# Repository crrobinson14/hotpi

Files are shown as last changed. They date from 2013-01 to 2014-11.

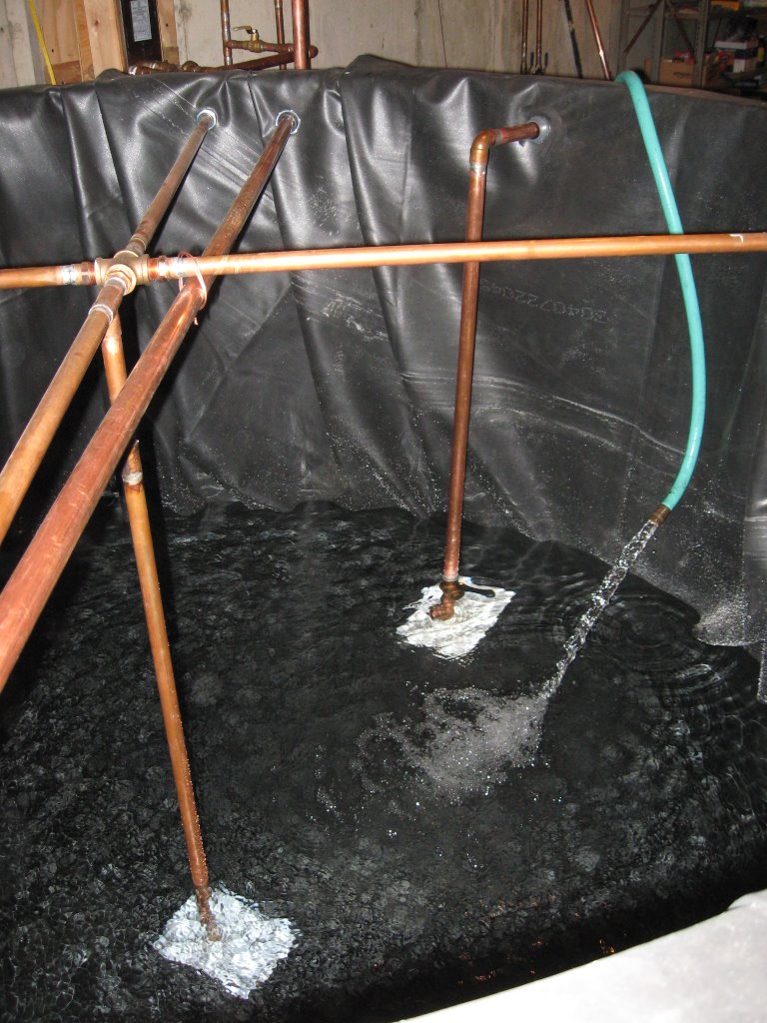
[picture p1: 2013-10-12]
photos/05 Lid Support.JPG

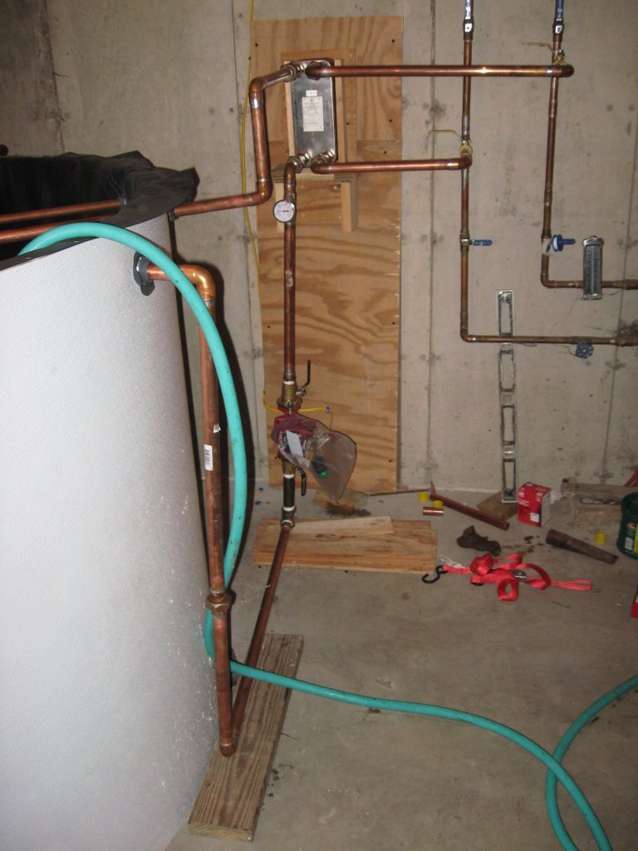
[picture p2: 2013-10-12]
photos/06 FlatPlate Plumbing.JPG

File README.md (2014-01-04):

hotpi
=====

HotPi is a Raspberry-Pi based heating control system. It is
designed to manage wood boilers, solar arrays, and other
alternative energy sources, although it is generic enough
that it could be programmed to control near any heating
and/or cooling system.

HotPi is Open Source Hardware (OSHW). That means it is not
a product - you must build it yourself, and you are solely
liable for its installation and programming. Included in
this project are circuit schematics, PCB layouts (with
Gerber files) for producing the boards, components lists,
documentation, and sample software.

For more information please see the project wiki:
https://github.com/crrobinson14/hotpi/wiki

LEGAL NOTICE: No warranties are made, expressed or implied,
as to the usability, merchantability, or performance of the
hardware or software provided in this project. All use is at
your own risk.

Analytics (https://github.com/igrigorik/ga-beacon)

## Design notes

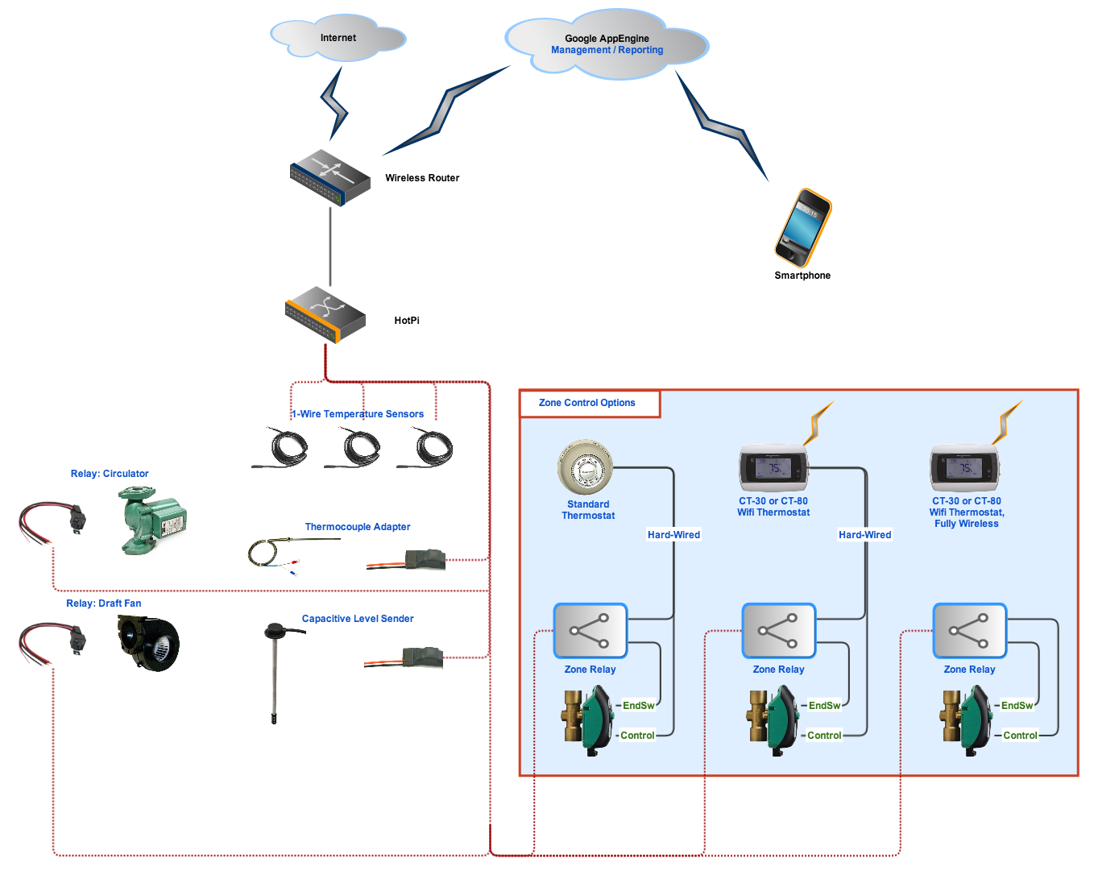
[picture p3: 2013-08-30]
docs/images/Overview.png

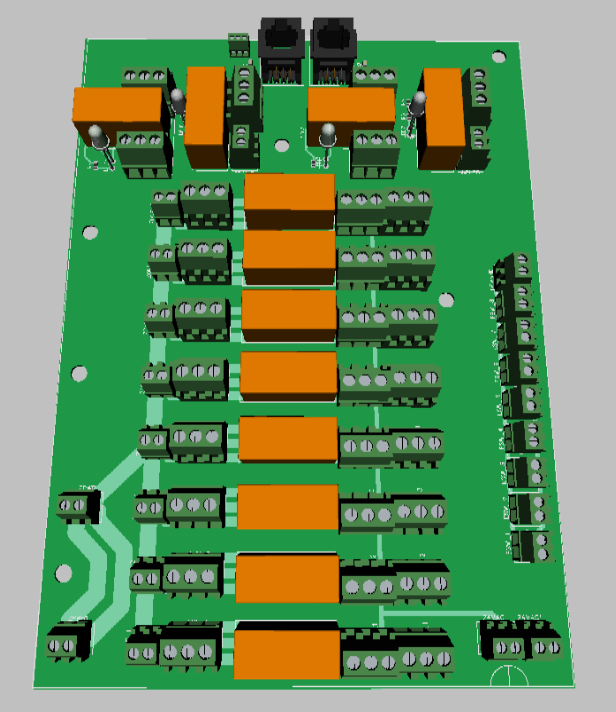
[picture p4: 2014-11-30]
pcb/zone/zone.png

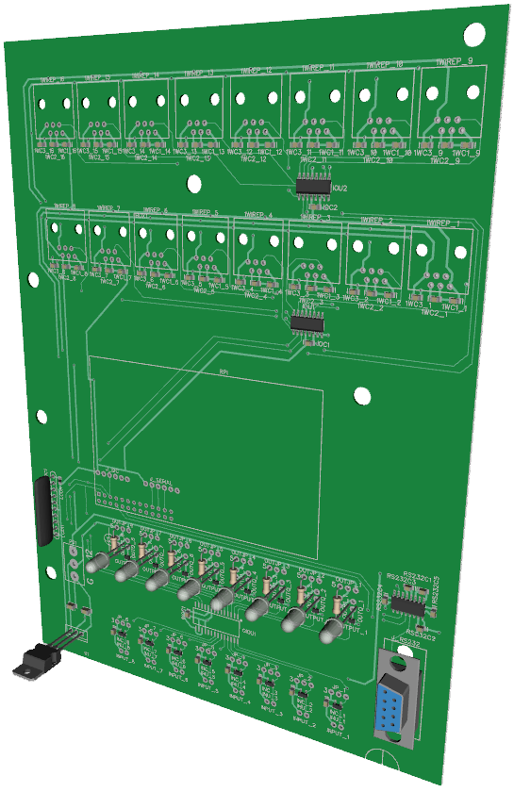
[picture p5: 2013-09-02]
pcb/hotpi/hotpi-3d.png

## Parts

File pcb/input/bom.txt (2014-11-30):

"RefDes","Value","Quantity","PartNumber"
"1WIRE2","","1","A-2014-1-4-R"
"C1","1u","1","C2012X7S2A105K"
"C2","0.1u","1","C0805C104K3RACTU"
"INPUT","","1",""
"LED1","GRN 2.2V 10mA","1","WP7113GD"
"R1","200","1","RMCF0805FT200R"
"R2","120","1","ERJ-6ENF1200V"
"RLY1","","1","RT424524"
"U2","","1","DS2413P+"

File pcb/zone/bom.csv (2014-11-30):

RefDes | Value | Quantity | PartNumber
1WACC |  | 1
1WIRE1 |  | 1 | A-2014-1-4-R
1WIRE2 |  | 1 | A-2014-1-4-R
24VAC |  | 1 | 282841-2
24VAC1 |  | 1 | 282841-2
AUX |  | 8 | 282841-3
BOX1 |  | 1 | TL412CP
C1 | 1u | 1 | C2012X7S2A105K
C2 | 0.1u | 1 | C0805C104K3RACTU
D3 |  | 1 | S1M-FDICT
D4 |  | 1 | S1M-FDICT
DEMAND |  | 1 | 282841-2
ESW |  | 8 | 282841-2
INPUTA |  | 1
INPUTB |  | 1
LED1 | GRN 2.2V 10mA | 1 | WP7113GD
LED2 | GRN 2.2V 10mA | 1 | WP7113GD
LED3 | ORG 2V 10mA | 1 | SLR-56DC3F
LED4 | ORG 2V 10mA | 1 | SLR-56DC3F
OUT1A |  | 1
OUT1B |  | 1
OUT2A |  | 1
OUT2B |  | 1
P1 |  | 1
P2 |  | 1
Q2 |  | 1 | DDTA113ZCA-7-F
Q3 |  | 1 | DDTA113ZCA-7-F
R1 | 1k 1/4W | 1 | RNCP0805FTD1K00
R2 | 120 | 1 | ERJ-6ENF1200V
R3 | 120 | 1 | ERJ-6ENF1200V
R4 | 1k 1/4W | 1 | RNCP0805FTD1K00
R5 | 200 | 1 | RMCF0805FT200R
R6 | 200 | 1 | RMCF0805FT200R
RLY1 |  | 1
RLY2 |  | 1 | RT424012
RLY3 |  | 1 | RT424524
RLY4 |  | 1 | RT424524
RLY6 |  | 8
TB |  | 8 | 282841-3
TT |  | 8 | 282841-3
U1 |  | 1 | DS2413P+
U2 |  | 1 | DS2413P+
ZONE |  | 8 | 282841-2
ZPWR |  | 1 | 282841-2
ZPWR1 |  | 1 | 282841-2

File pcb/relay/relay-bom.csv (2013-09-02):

# | Quantity | Type | Value | PartNumber | RefDes
1 | 1 | JP3 |  |  | 1WACC
2 | 2 | RJ12 |  | A-2014-1-4-R | 1WIRE1, 1WIRE2
3 | 1 | CAP_0805 | 1u | C2012X7S2A105K | C1
4 | 1 | CAP_0805 | 0.1u | C0805C104K3RACTU | C2
5 | 1 | 1N4007 |  | S1M-FDICT | D1
6 | 1 | TERM2 |  |  | INPUT
7 | 1 | JP6 |  |  | JP1
8 | 1 | LED | GRN 2.2V 10mA | WP7113GD | LED1
9 | 1 | LED | ORG 2V 10mA | SLR-56DC3F | LED2
10 | 3 | TERM3 |  |  | OUTPUT1, OUTPUT2, P1
11 | 1 | DDTA113 |  | DDTA113ZCA-7-F | Q4
12 | 1 | RES_0805 | 200 | RMCF0805FT200R | R1
13 | 1 | RES_0805 | 120 | ERJ-6ENF1200V | R2
14 | 1 | RES_0805 | 1k 1/4W | RNCP0805FTD1K00 | R3
15 | 1 | RT2 |  | RT424524 | RLY1
16 | 1 | RT1 |  | RT424012 | RLY2
17 | 1 | DS2413 |  | DS2413P+ | U2
 | 20

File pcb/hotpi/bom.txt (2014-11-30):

"RefDes","Value","Quantity","PartNumber"
"1WC1","0.1u","16","C0805C104K3RACTU"
"1WC2","0.1u","16","C0805C104K3RACTU"
"1WC3","0.1u","16","C0805C104K3RACTU"
"1WIREP","","16","A-2014-1-4-R"
"BOX1","","1","TL412CP"
"C1","10u TANT","1","399-3684-1"
"C2","10u TANT","1","399-3684-1"
"IOC1","0.1u","1","C0805C104K3RACTU"
"IOC2","0.1u","1","C0805C104K3RACTU"
"IOU1","","1","DS2482S-800"
"IOU2","","1","DS2482S-800"
"PS1","","1","282841-3"
"U1","3.3V","1","LM1117T-3.3/NOPB"
"U2","","1",""
"U3","","1",""

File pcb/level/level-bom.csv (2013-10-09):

# | Quantity | Type | Value | PartNumber | RefDes
1 | 2 | JP3 |  |  | JP1, JP2
2 | 12 | RES_0805 | 470 | RMCF0805FT470R | R1, R2, R3, R4, R5, R6, R7, R8, R9, R10, R11, R12
3 | 12 | REED |  | ORD324-1015 | SW1, SW2, SW3, SW4, SW5, SW6, SW7, SW8, SW9, SW10, SW11, SW12
 | 26

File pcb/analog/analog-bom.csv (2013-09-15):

# | Quantity | Type | Value | PartNumber | RefDes
1 | 3 | JP3 |  |  | 1WACC, JP2, JP3
2 | 2 | RJ12 |  | A-2014-1-4-R | 1WIRE1, 1WIRE2
3 | 1 | CAP_0805 | 1u | C2012X7S2A105K | C1
4 | 6 | CAP_0805 | 0.1u | C0805C104K3RACTU | C2, C3, C9, C10, C12, C13
5 | 1 | CAP_0805 | 10u TANT | 399-3684-1 | C11
6 | 1 | JP6 |  |  | JP1
7 | 2 | TERM2 |  | 282841-2 | P1, P2
8 | 1 | RES_1206 | .02 | LVK24R020DER | R1
9 | 2 | RES_0805 | 0.30 | 311-.30SCT | R2, R5
10 | 1 | RES_0805 | 1M | RMCF0805FT1M00CT | R7
11 | 1 | DS2756E+ |  | DS2756E+ | U1
12 | 1 | AD849x |  | AD8495ARMZ | U2
 | 22

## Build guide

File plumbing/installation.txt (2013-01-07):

Oil Boiler
----------
1. Install a pair of 1" Tees (A) on the inlet/outlet of the oil boiler. On the
outlet side, this may also require a new 1" MIP to sweat (B).

2. Plumb both Tees with 1" copper pipe (C) to a pair of 1" sweat-to-PEX adapters
(D), then with 1" PEX (E) to a pair of ball valves (F).

3. Cut the 1/2" cold water supply line to the furnace at a convenient spot along
its horizontal run. Cut the pipe again in the vertical section to remove the
double-elbow transition from horizontal to vertical.

4. Assemble a short "H" bypass with a ball valve (F) and two Tees (Q). Add a
pair of ball valves (F) on the top of each leg.

5. Solder a Tee (I) onto the horizontal run, then run a vertical pipe (J) to a
1/2"-1" reducer (K) and fitting (D) into one leg of the bypass. Plumb the
vertical inlet line to the other bypass leg using a reducer (K) and fitting (D).

5. Cut the cold water inlet to the mixing valve just past the elbow below the
valve. Cap (L) the remaining section past the low-water drain valve.

6. De-solder the elbow from the cold water inlet to retain as much stub as
possible, and clean up the end (discard the elbow). Rotate the stub to a
45-degree angle and use a coupling (M) and elbow (N) to plumb this to the cold
water supply Tee.

7. Plumb PEX lines from all four ball valves over to the hot water storage tank
using tube supports (O) and bend supports (P). On the boiler lines, install a
pair of check valves (G) with fittings (H) such that the flow arrow points
TOWARD the boiler on the HOT line, and the flow arrow points AWAY from the
boiler on the COLD line.

8. For now, close all four ball valves leading to the hot water storage tank,
then open the ball valve between the Tees on the DHW coil inlet. Re-charge the
system and verify that the oil boiler correctly heats the house and hot water.

A - 2 - 1" Copper Tee - http://www.pexsupply.com/Cello-WPT-16-1-CxCxC-Tee-1056000-p
B - 1 - 1" MIP to sweat - http://www.pexsupply.com/Cello-WP4-16-1-Copper-X-Male-Adapter-1024000-p
C - 1 - 1" x 2' Copper Pipe - http://www.pexsupply.com/Kobe-Wieland-100-20-MCP-1-x-2-Type-M-Straight-Copper-Pipe
D - 4 - 1" Sweat to PEX - http://www.pexsupply.com/HydroPEX-H021000-1-PEX-x-1-Copper-Pipe-Brass-Adapter-3755000-p
E - 1 - 1" Barrier PEX - http://www.pexsupply.com/Rifeng-100-300-OXY-1-Oxygen-Barrier-PEX-Tubing-300-ft-Coil
F - 5 - 1" Ball Valve - http://www.pexsupply.com/HydroPEX-H081000-1-PEX-x-1-PEX-Ball-Valve-5882000-p
G - 2 - Check Valve - http://www.pexsupply.com/Hydrovalve-SC100T-1-Threaded-Swing-Check-Valve
H - 4 - 1" MIP to PEX - http://www.pexsupply.com/HydroPEX-H031000-1-PEX-x-1-NPT-Brass-Male-Adapter-3747000-p
I - 1 - 1/2" Copper Tee - http://www.pexsupply.com/Cello-WPT-08-1-2-CxCxC-Tee-1054000-p
J - 1 - 5' 1/2" Copper Pipe - http://www.homedepot.com/h_d1/N-5yc1v/R-100558487/h_d2/ProductDisplay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
K - 2 - 1/2" to 1" Sweat - http://www.pexsupply.com/Cello-WP0-16-08-1-x-1-2-CxC-Coupling-3588000-p
L - 1 - 1/2" Cap - http://www.pexsupply.com/Cello-WP17-08-1-2-Copper-Cap-951000-p
M - 1 - 1/2" Copper Coupling - http://www.pexsupply.com/Cello-WP0-08-1-2-CxC-Coupling-1188000-p
N - 1 - 1/2" Elbow - http://www.pexsupply.com/Cello-WP7-08-1-2-CxC-90-Elbow-896000-p
O - 1 - 1" Tube Support, Box - http://www.pexsupply.com/Sioux-Chief-555-4-Tube-Talon-for-1-PEX-Tubing-Bag-of-50-2207000-p
P - 8 - 1" Bend Support - http://www.pexsupply.com/Viega-51060-1-PEX-Plastic-Bend-Support-12534000-p
Q - 2 - 1" PEX Tee - http://www.pexsupply.com/HydroPEX-H051000-1-PEX-x-1-PEX-x-1-PEX-Brass-Tee-3728000-p

Storage Tank
------------
1. Plumb the boiler "hot" line into the outlet side of an air scoop (A) using a
pair of 1" fittings (B). Install a vent (C) and expansion tank (D) on the air
scoop.

2. On both hot and cold above the tank, add a pair of Tees (E) horizontally,
with the stubs pointing down at a convenient point to run down to the tank. Put
a ball valve (F) on the other side of each Tee. Do the same for the domestic hot
water, but use elbows instead (G).

3. Fabricate a DHW heat exchanger by cutting a 6-port manifold (H) in half and
capping (I) one cut end, then installing a pair of sweat fittings (J). Cut one
7' and two 8.5' lengths from a coil of 1/2" tubing (K) and solder these
between the two manifolds, bending the two longer lengths outward as necessary.
Suspend this coil in the tank approx. 6" below the top lip.

4. Plumb this heat exchanger through two bends and a pair of elbows (G) out
through holes in the top lip of the tank and then up to the DHW hot/cold lines.

5. Fabricate the boiler heat exchanger coils by cutting the remaining tubing
into two 18' lengths, and then the next coil into two 24' lengths and two 6'
lengths. Coil these tubes as necessary to service the four corners and two long
sides of the tank. Solder these to two more manifolds (H).

6. Plumb both manifolds similarly to the DHW setup, using sweat fittings (J) to
run the lines out to a pair of elbows (G), but add an additional elbow on the
bottom (cold) line to make the direction change. Also, insulate (L) the cold
line as much as possible. Run the "hot" line directly up to the appropriate Tee.

7. On the cold side, run the line back down again outside the tank to a Tee (E)
and then to a pair of elbows (G) to create two branches. Connect one leg to a
zone valve (M) using a pair of fittings (B), with the flow direction pointing
DOWN. Connect the other leg to a circulator (N) using a pair of flanges (O)
and fittings (B).

8. Connect both branches down to the stubs of a pair of Tees (E). Connect these
Tees together, then run one line to a ball valve (F) low point drain, and the
other through an elbow (G) and up to the hot-line Tee.

9. Use 1/2" CPVC tubing plus Tee and Elbow fittings to build a support framework
for the heat exchangers. Then build two 1" CPVC stubs with elbows through the
top lip of the tank. One stub should go nearly to the bottom of the tank
(intake) while the other should end as close to the top of the tank as possible.

10. Build a thermostat dip tube from 1/2" CPVC by capping one end and using an
elbow on the other. Install two temperature sensors in the tube, one near the
top and the other near the bottom, with heat-shrink on the connections to
prevent them from shorting one another out. Fill the tube with mineral oil.

11. Seal all tank holes with silicone. Slowly charge each heat exchanger and
check carefully for leaks. Fix any leaks, using compressed air to blow out the
lines if necessary. Then fill the tank and check the tank itself for leaks. Once
everything is ready to go, close back off the oil burner heat lines but leave
the DHW lines open.

A - 1 - Air Scoop - http://www.pexsupply.com/Taco-431-6-1-Air-Scoop-3512000-p
B - 6 - 1" MIP to PEX - http://www.pexsupply.com/HydroPEX-H031000-1-PEX-x-1-NPT-Brass-Male-Adapter-3747000-p
C - 1 - Air Vent - http://www.pexsupply.com/Taco-400-4-1-8-Hy-Vent
D - 1 - Exp. Tank - http://www.ebay.com/itm/Flexcon-HTX-30-4-1-2-gal-Hydronic-Expansion-Tank-/130746785428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
E - 5 - 1" PEX Tee - http://www.pexsupply.com/HydroPEX-H051000-1-PEX-x-1-PEX-x-1-PEX-Brass-Tee-3728000-p
F - 3 - 1" Ball Valve - http://www.pexsupply.com/HydroPEX-H081000-1-PEX-x-1-PEX-Ball-Valve-5882000-p
G - 10 - 1" PEX Elbow - http://www.pexsupply.com/HydroPEX-H001000-1-PEX-x-1-PEX-Brass-Elbow-3701000-p
H - 3 - 6-port Manifold - http://www.ebay.com/itm/6-Outlet-Copper-Manifold-by-Alberta-Custom-Tee-1-x-6-1-2-Ports-/190663487818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
I - 1 - 1" Cap - http://www.pexsupply.com/Cello-WP17-16-1-Copper-Cap-953000-p
J - 4 - 1" Sweat to PEX - http://www.pexsupply.com/HydroPEX-H021000-1-PEX-x-1-Copper-Pipe-Brass-Adapter-3755000-p
K - 2 - 1/2" 60' Tubing - http://www.homedepot.com/Plumbing-Pipes-Fittings-Valves-Copper-Pipe-Fittings-Pipe/h_d1/N-25ecodZ5yc1vZ25ecodZ25ecodZ25ecodZbuyt/R-202504352/h_d2/ProductDisplay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
L - ? - Insulation - http://www.lowes.com/pd_24434-1410-P12XB/6_0__?productId=3133247
M - 1 - Zone Valve - http://www.pexsupply.com/Taco-Z100T2-1-1-Zone-Sentry-Valve-Threaded
N - 1 - Taco 007 - http://www.pexsupply.com/Taco-007-F5-007-Cast-Iron-Circulator-1-25-HP-1983000-p
O - 1 - Taco Flange - http://www.pexsupply.com/Taco-110-252F-1-Taco-Iron-Freedom-Flange-Pair-1974000-p

Wood Boiler
-----------
1. Plumb the hot-side line above the wood boiler and into a Tee (A) with the
stub pointing to the right. Connect the bottom of the Tee into the boiler via
a threaded fitting (B). Stub the Tee over to the right side of the boiler,
through an elbow, and down to a zone valve (D) via a pair of fittings (B).
The flow direction on the zone valve should point down.

2. Plumb the cold-side line across to the right side of the wood boiler and
down nearly (6") to the floor, into the stub of a Tee (A). Connect the right
side of the Tee to a ball valve (E) low point drain. Connect the left side to
the right side of another Tee (A). The stub of this Tee should connect to the
zone valve from Step 1 above.

3. Connect the next leg of the tees into an elbow and up into a circulator (F)
via a flange (G) and a pair of fittings (B). Support the circulator with a block
of wood.

4. Connect the top of the circulator through a pair of elbows (C) around the
back of the wood boiler and into a Tee (A) and a final elbow (C) and into the
inlets of the boiler via a pair of fittings (B).

5. Install a relief valve on a short iron pipe stub in the pressure-relief hole
on top of the boiler.

6. Connect the boiler's flue as required.

7. Fill the boiler with water and check for leaks in the entire system. Then
test fire the boiler with a SMALL load of wood with a thermometer in the
temperature well in the top of the water jacket. If the temperature reaches an
unacceptable level, force the circulator to turn on and dump heat into the water
tank.

A - 4 - 1" PEX Tee - http://www.pexsupply.com/HydroPEX-H051000-1-PEX-x-1-PEX-x-1-PEX-Brass-Tee-3728000-p
B - 7 - 1" MIP to PEX - http://www.pexsupply.com/HydroPEX-H031000-1-PEX-x-1-NPT-Brass-Male-Adapter-3747000-p
C - 4 - 1" PEX Elbow - http://www.pexsupply.com/HydroPEX-H001000-1-PEX-x-1-PEX-Brass-Elbow-3701000-p
D - 1 - Zone Valve - http://www.pexsupply.com/Taco-Z100T2-1-1-Zone-Sentry-Valve-Threaded
E - 3 - 1" Ball Valve - http://www.pexsupply.com/HydroPEX-H081000-1-PEX-x-1-PEX-Ball-Valve-5882000-p
F - 1 - Taco 007 - http://www.pexsupply.com/Taco-007-F5-007-Cast-Iron-Circulator-1-25-HP-1983000-p
G - 1 - Taco Flange - http://www.pexsupply.com/Taco-110-252F-1-Taco-Iron-Freedom-Flange-Pair-1974000-p
H - 1 - Relief Valve - Home Depot
Z - 1 - 3/4" Iron Pipe - Home Depot

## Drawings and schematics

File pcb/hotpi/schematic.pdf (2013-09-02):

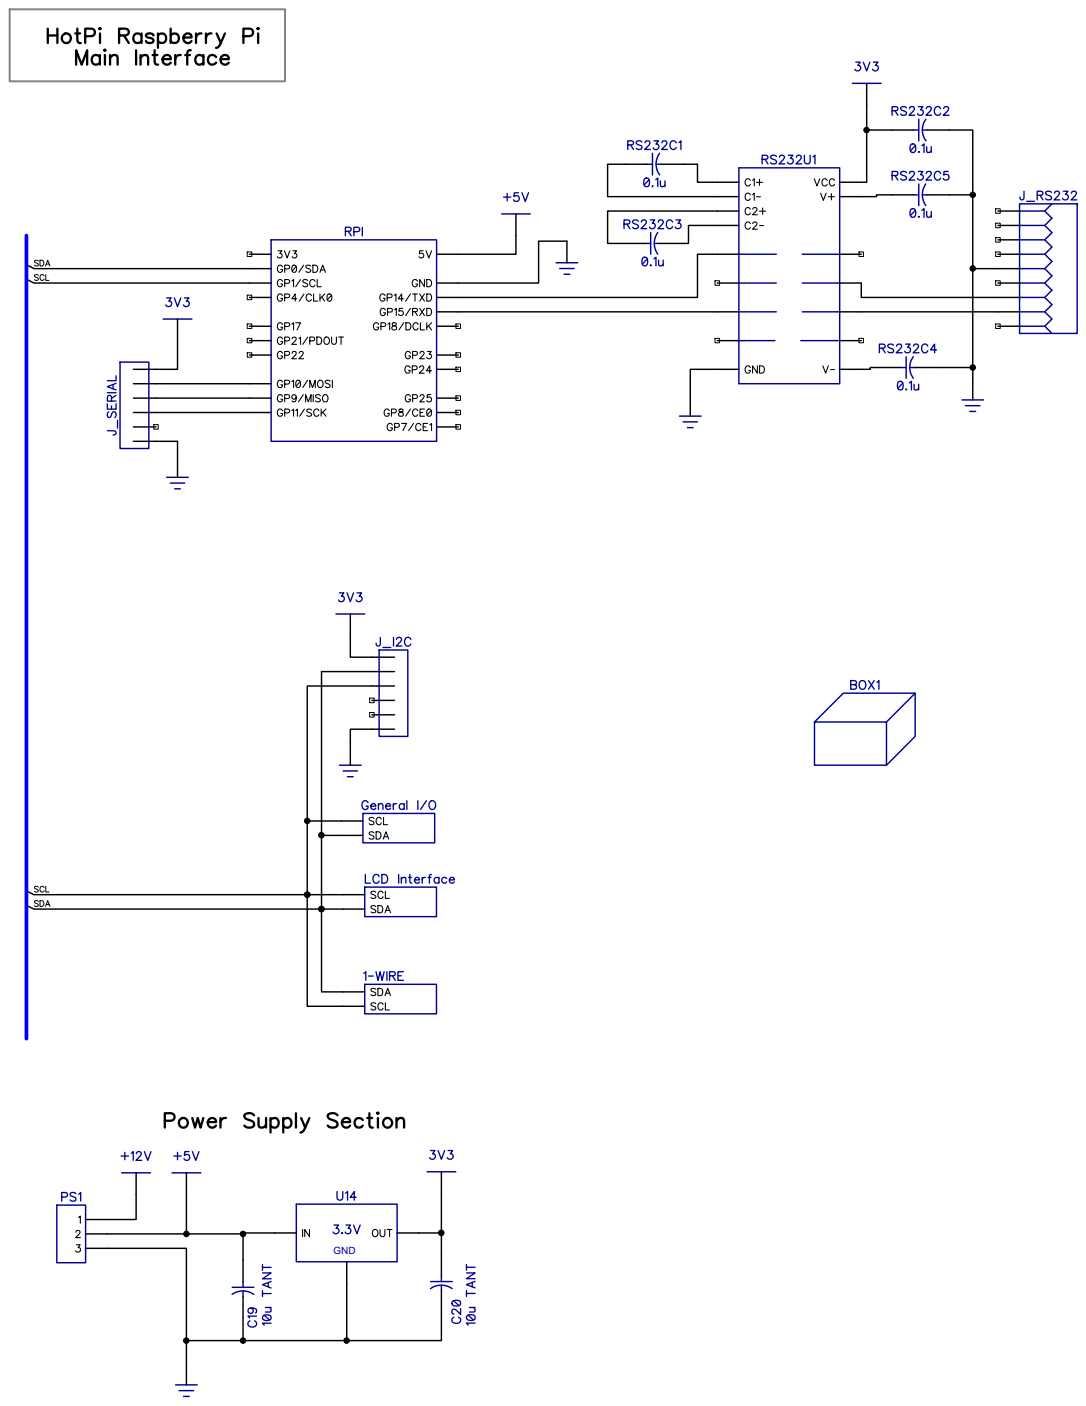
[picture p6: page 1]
GND

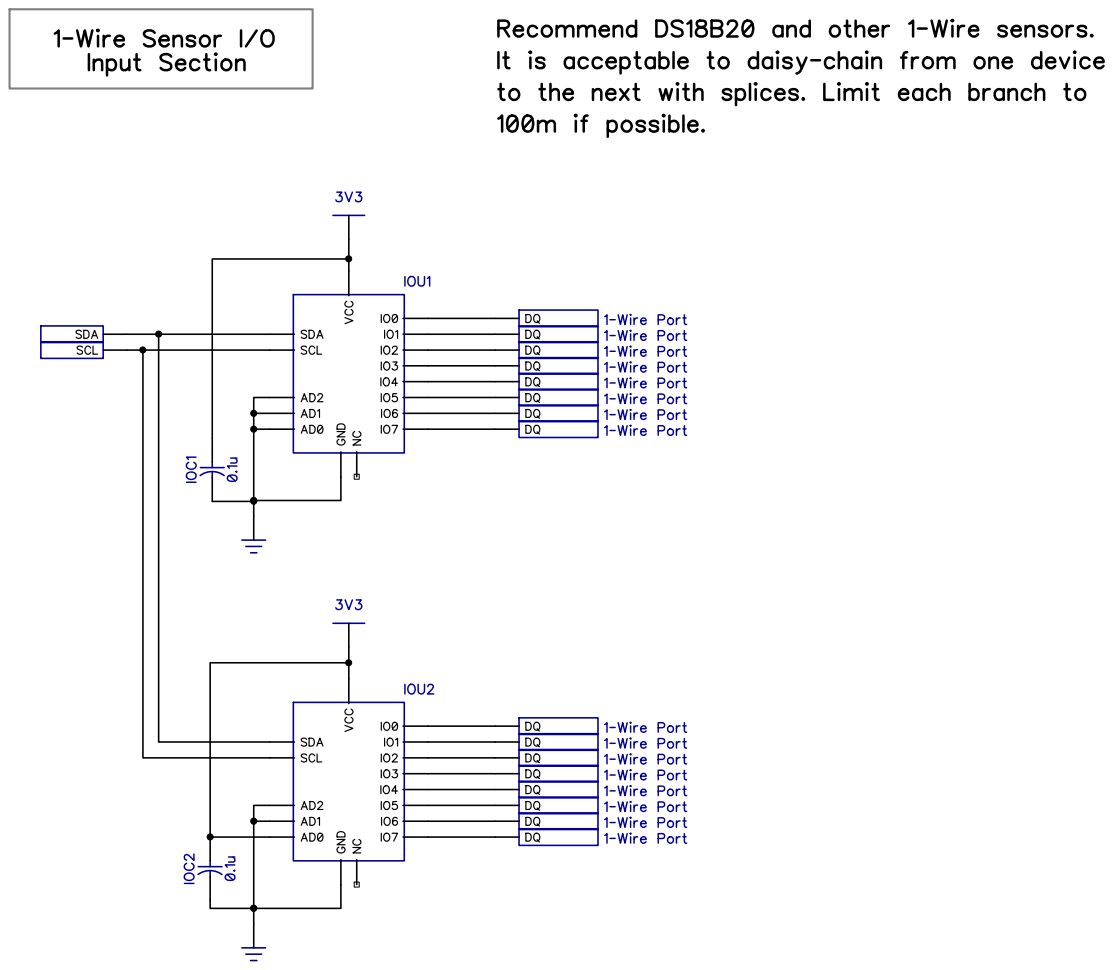
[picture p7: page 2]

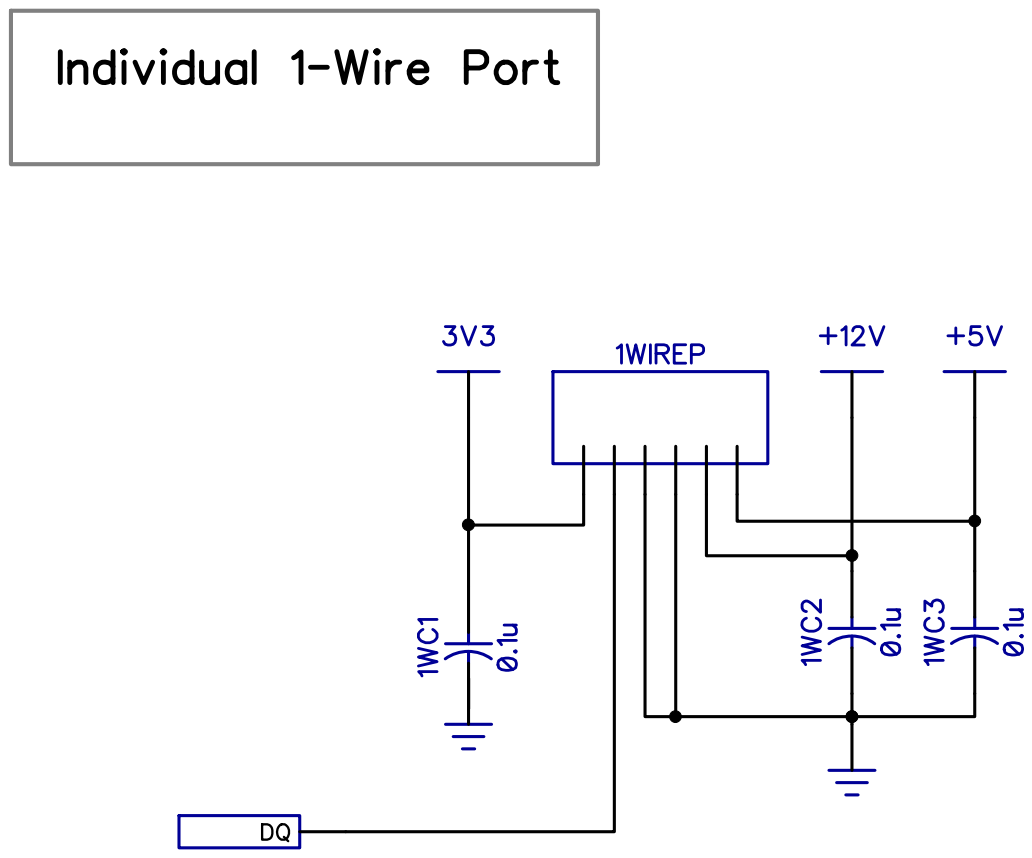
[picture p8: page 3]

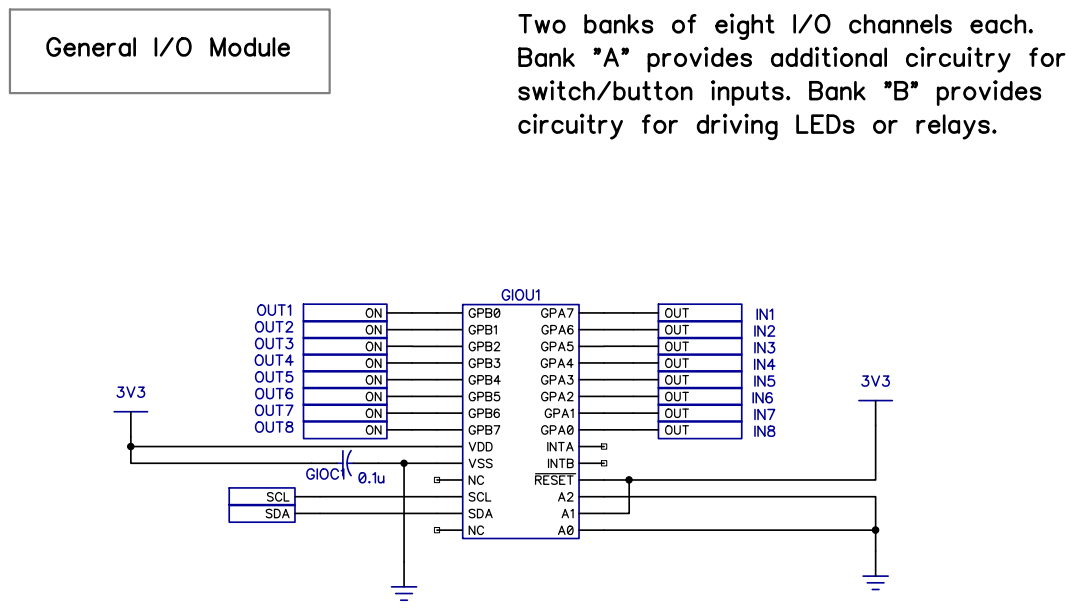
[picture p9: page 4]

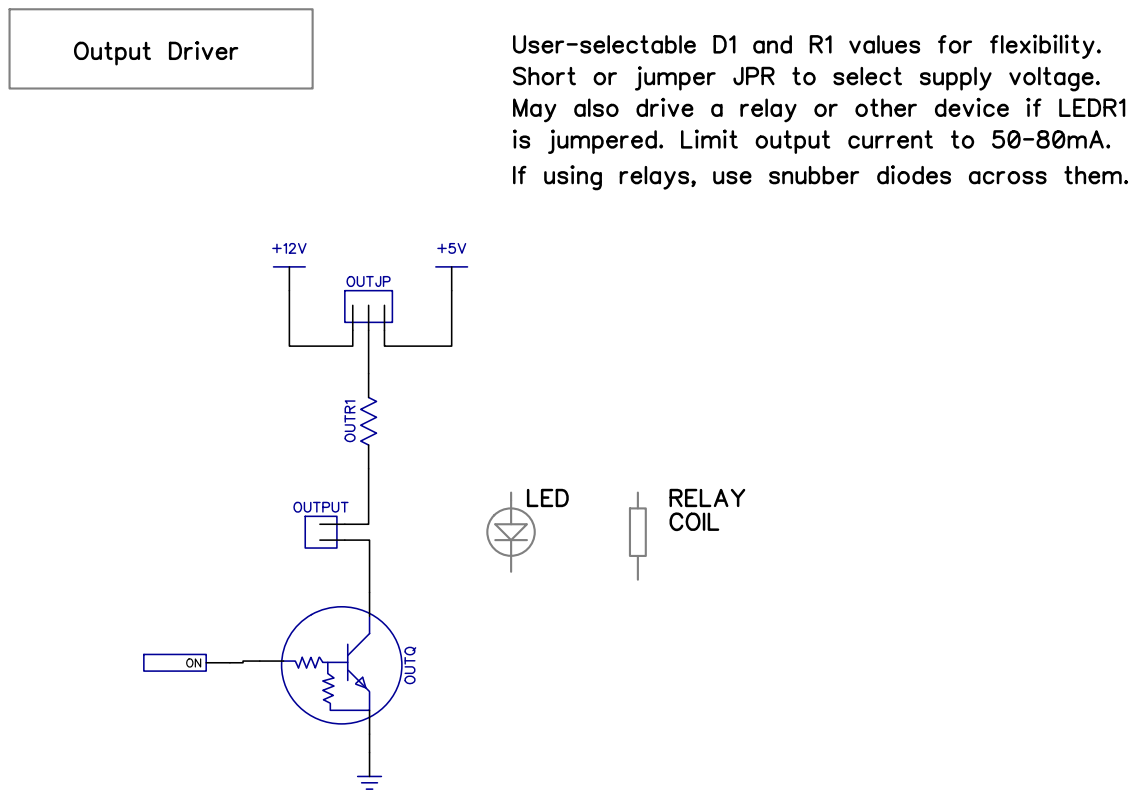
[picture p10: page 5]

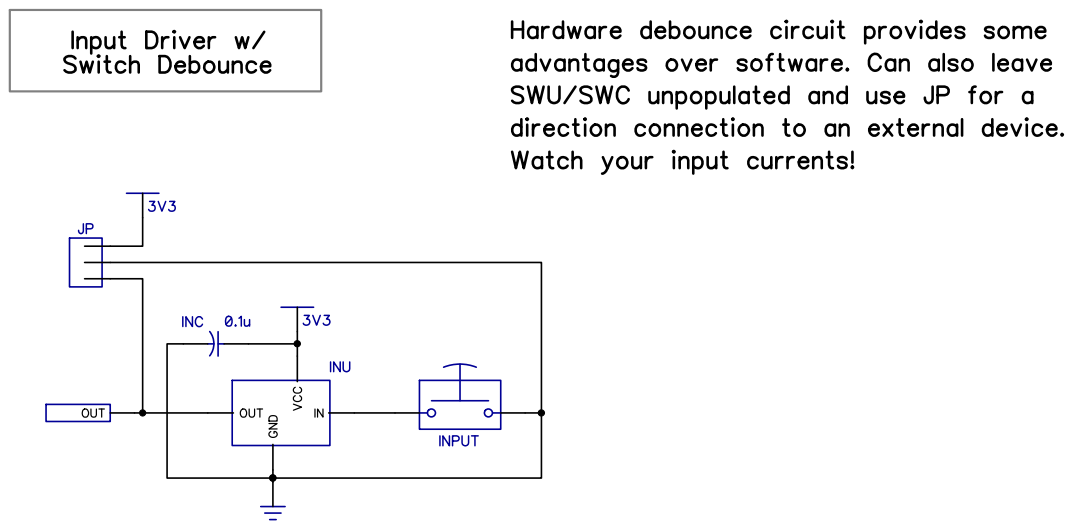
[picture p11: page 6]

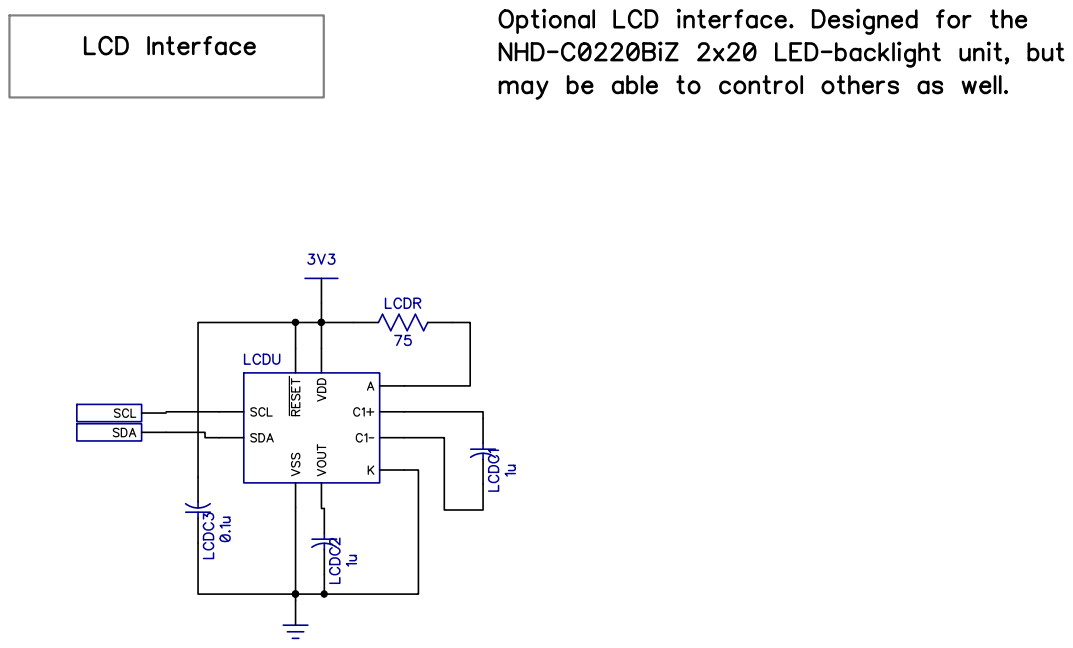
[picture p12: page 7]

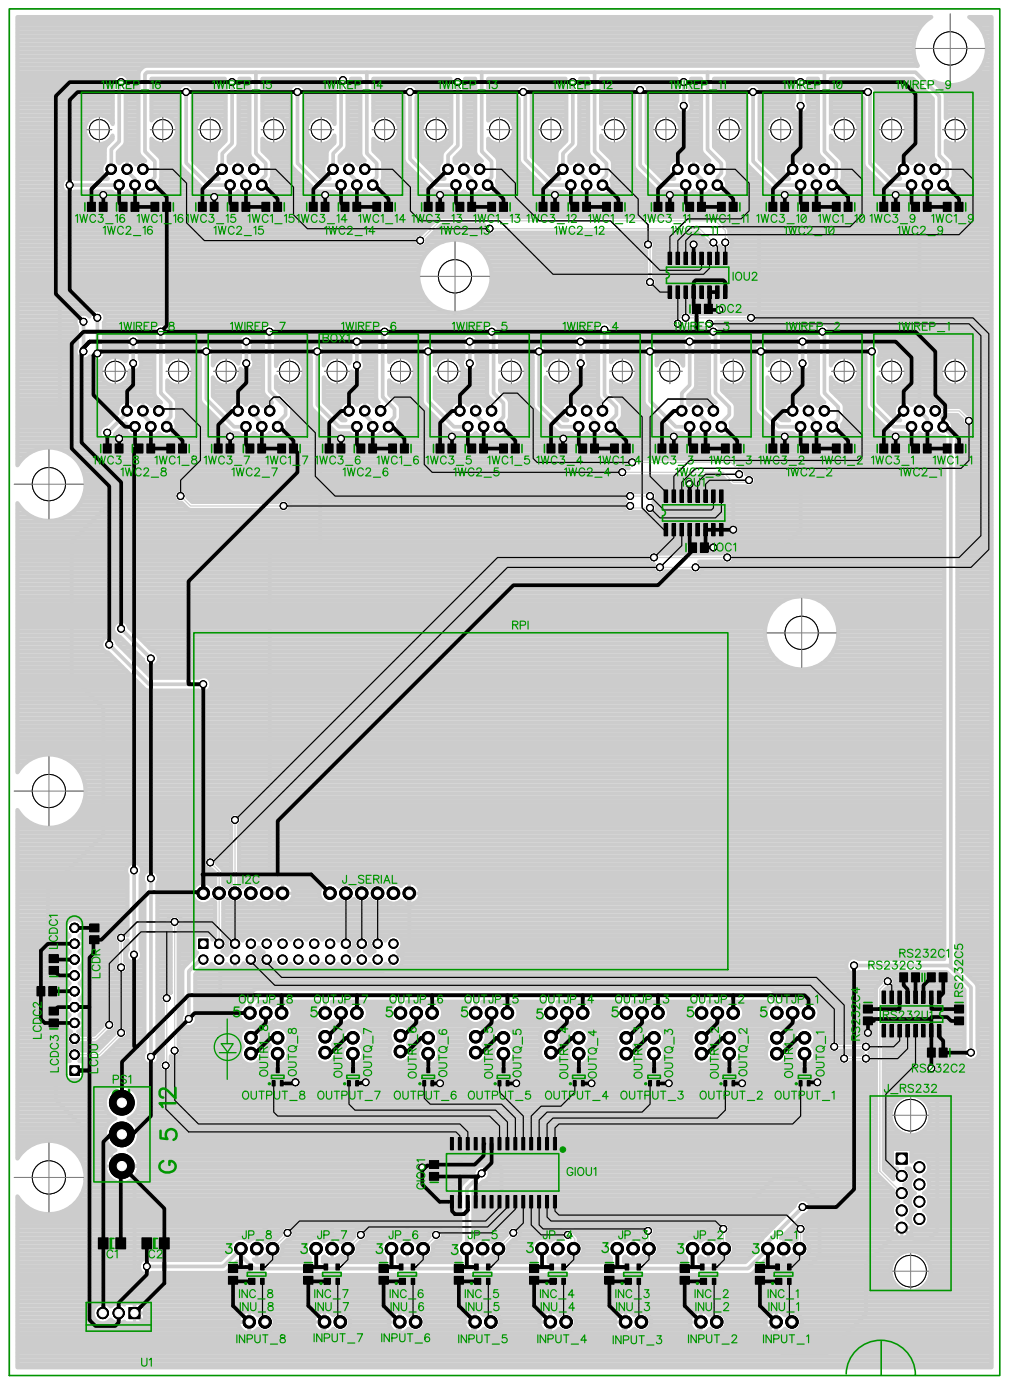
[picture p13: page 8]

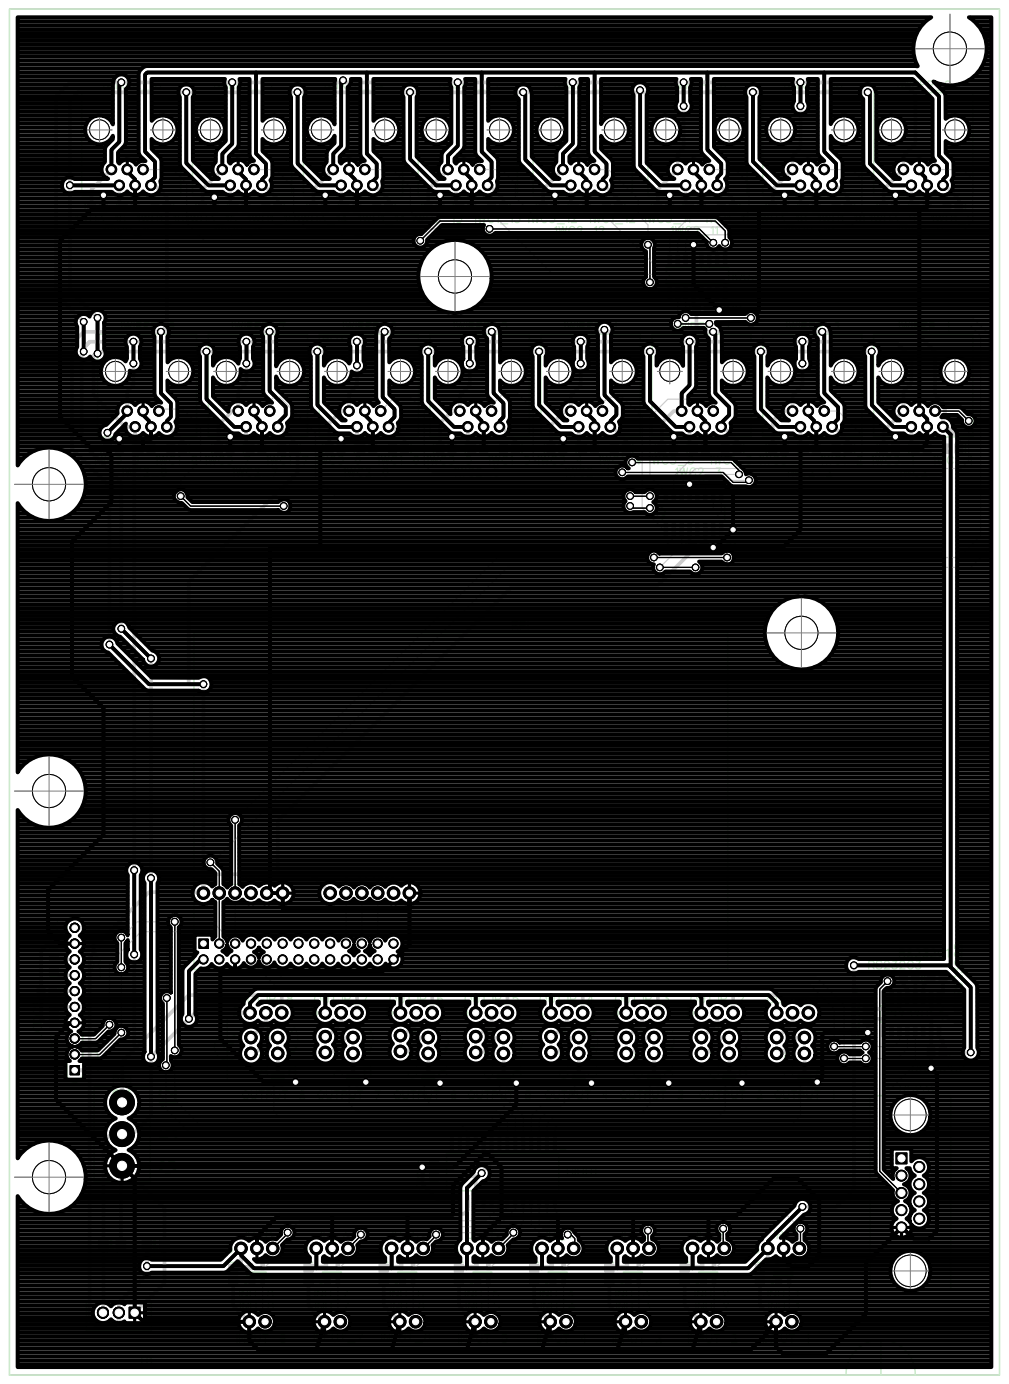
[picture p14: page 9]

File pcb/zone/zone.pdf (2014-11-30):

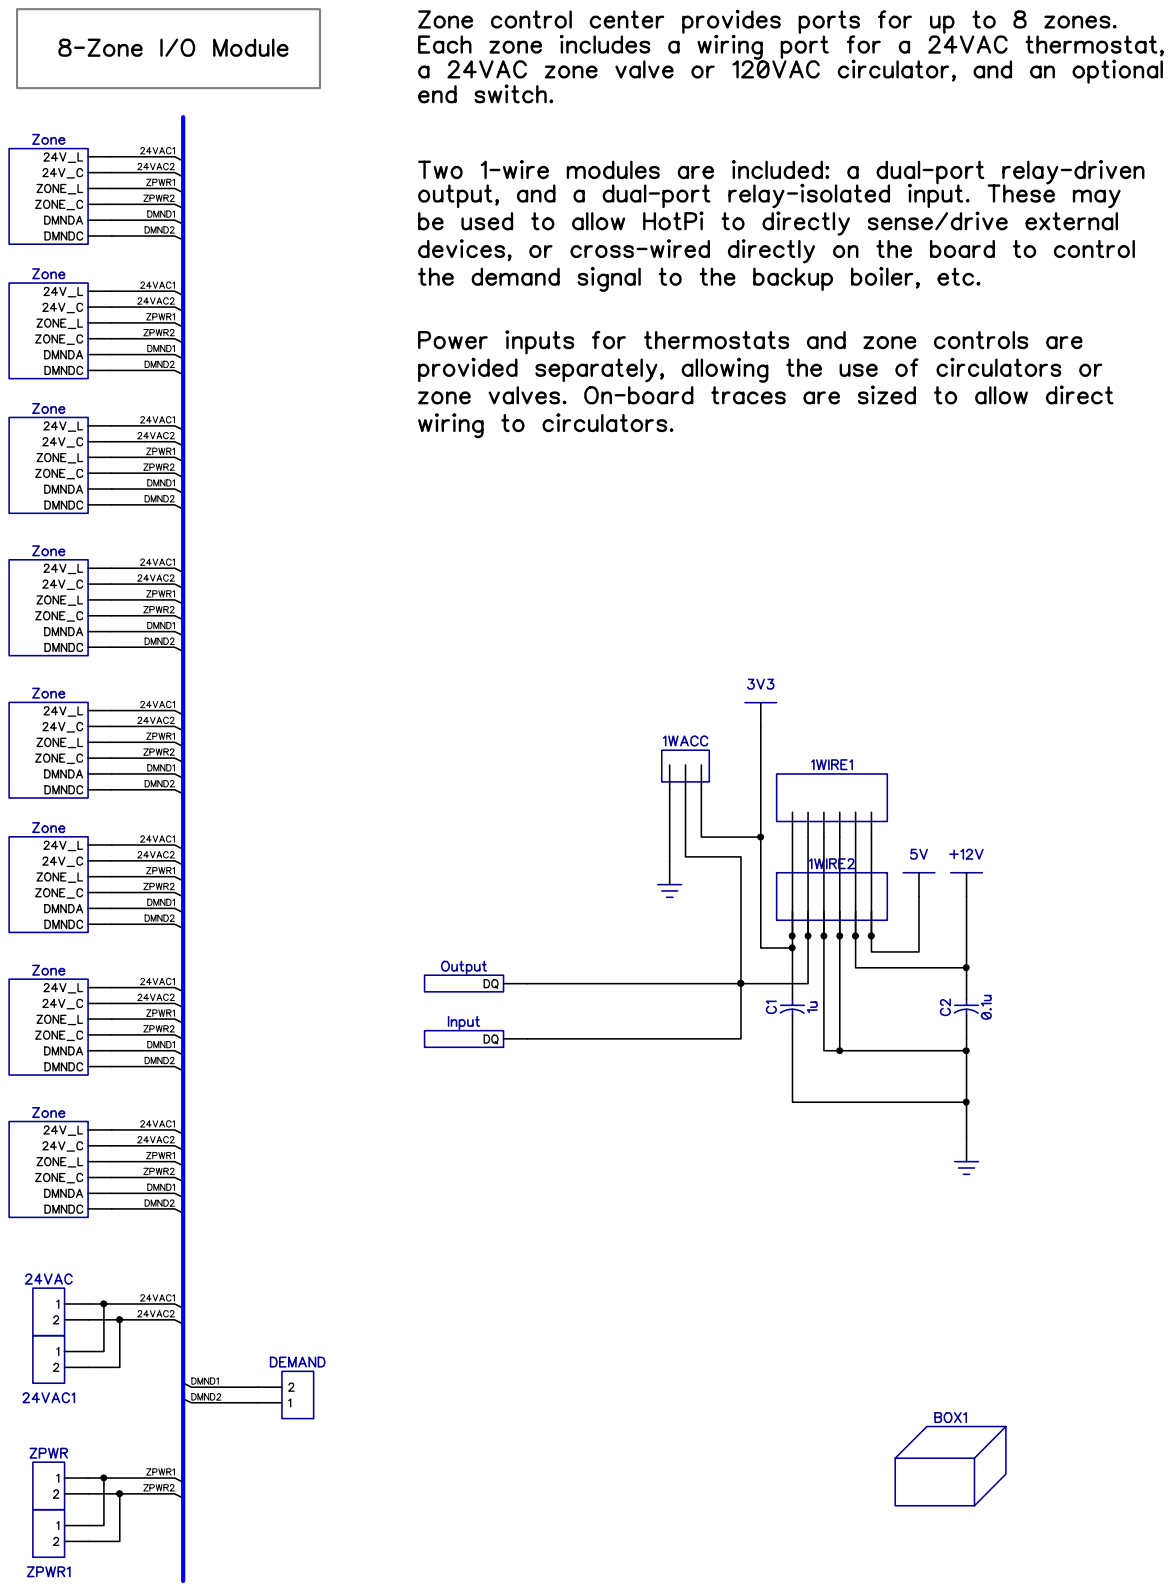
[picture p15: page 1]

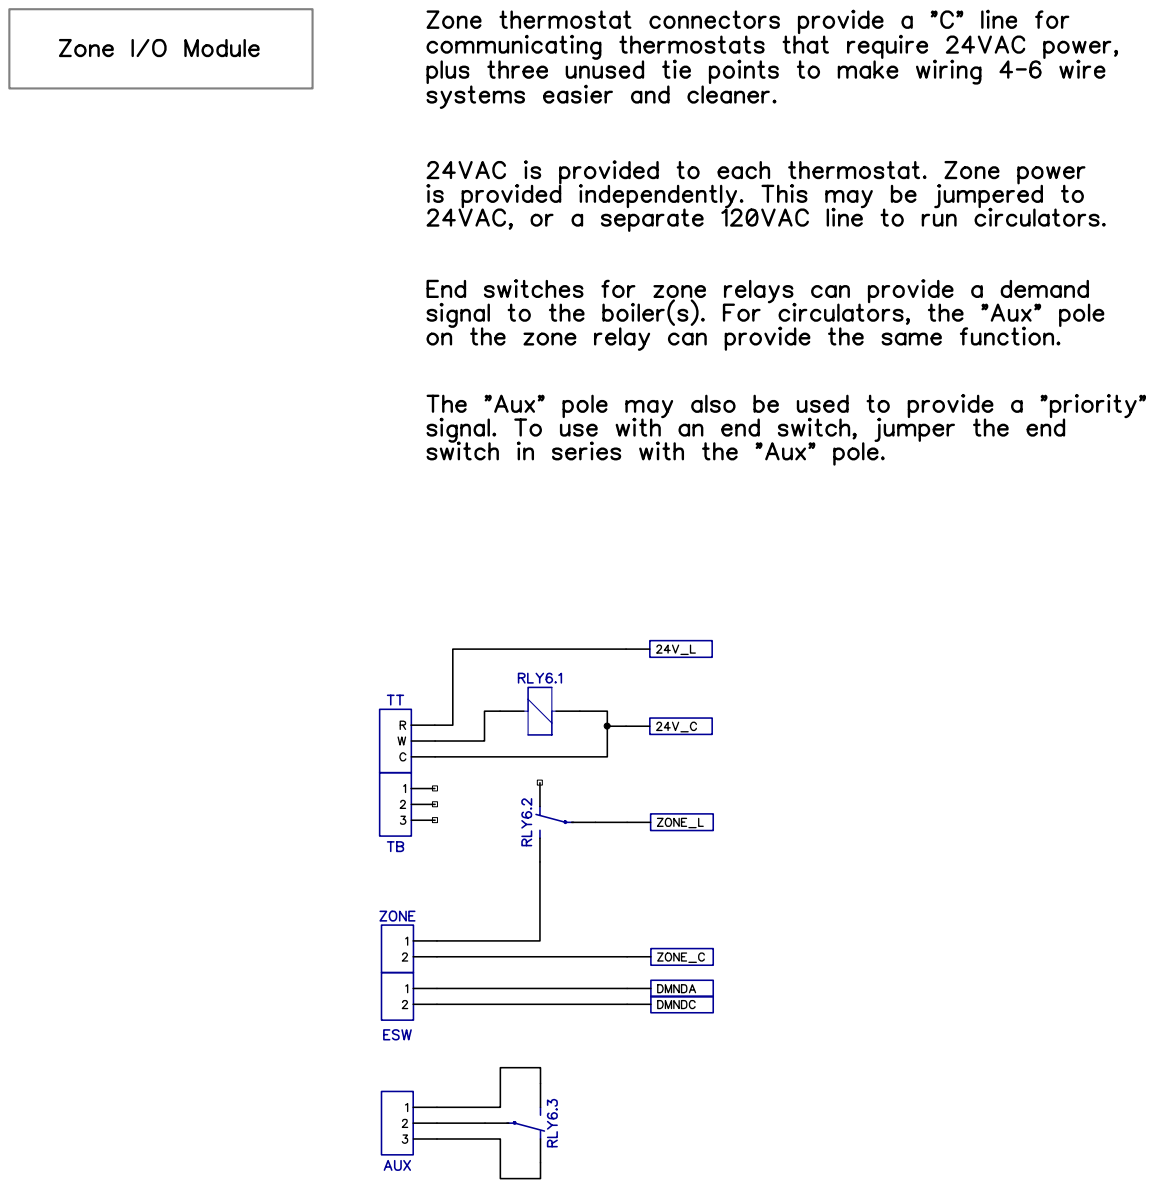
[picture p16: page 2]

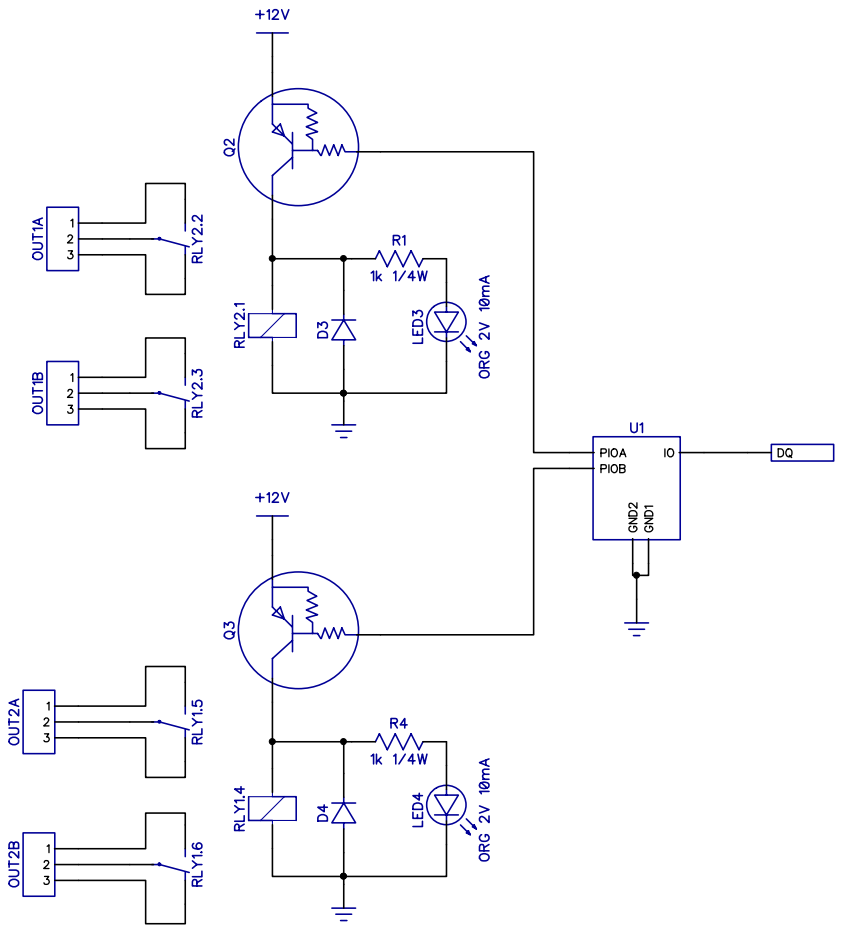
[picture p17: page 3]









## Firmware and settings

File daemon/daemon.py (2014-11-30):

import time
from config import hotpiConfig
from lib.devices import deviceManager
from lib.files import *

dmgr = deviceManager()
thermostats = ['tstatdown', 'tstatbed', 'tstatfront']
#zones = ['zonedown', 'zonebed', 'zonefront']
zones = ['zonedown', 'zonebed']

while True:
    dmgr.poll()

    tstatbed = hotpiConfig['devices']['tstatbed']['handler']
    tstatdown = hotpiConfig['devices']['tstatdown']['handler']
    tstatfront = hotpiConfig['devices']['tstatfront']['handler']
    tstatbed = hotpiConfig['devices']['tstatbed']['handler']
    woodcirc = hotpiConfig['devices']['woodcirc']['handler']
    wooddraft = hotpiConfig['devices']['wooddraft']['handler']

    zonedown = hotpiConfig['devices']['zonedown']['handler']
    zonefront = hotpiConfig['devices']['zonefront']['handler']
    zonebed = hotpiConfig['devices']['zonebed']['handler']

    coldstart = hotpiConfig['devices']['coldstart']['handler']
    quietmode = hotpiConfig['devices']['quietmode']['handler']
    endcycle = hotpiConfig['devices']['endcycle']['handler']

    # dmgr.get('wooddraft').set(0)

    boilertemp = int(dmgr.get('boilertemp').status['temperature'])
    returntemp = int(dmgr.get('returntemp').status['temperature'])
    [dmgr.get(t).setMessage(boilertemp) for t in thermostats]

    # Force all the zones open for now
    [dmgr.get(z).set(1) for z in zones]

    demand = (tstatbed.status['temp'] < 71)
    # demand = True;

    USEDRAFT = 1 if quietmode.state is 0 else 0

    if boilertemp < 125:
        # Below 125 we assume the boiler is off
        if coldstart.state is 1:
            dmgr.globalstat = "Below 125 (COLD START)"
            [dmgr.get(t).setLEDs(0) for t in thermostats]
            dmgr.get('woodcirc').set(0)
            dmgr.get('wooddraft').set(USEDRAFT)
        else:
            dmgr.globalstat = "Below 125 (Offline)"
            [dmgr.get(t).setLEDs(0) for t in thermostats]
            dmgr.get('woodcirc').set(0)
            dmgr.get('wooddraft').set(0)

    elif boilertemp < 145:
        if coldstart.state is 1:
            dmgr.globalstat = "Below 145 (COLD START)"
            [dmgr.get(t).setLEDs(0) for t in thermostats]
            dmgr.get('woodcirc').set(0)
            dmgr.get('wooddraft').set(USEDRAFT)
        elif endcycle.state is 1:
            dmgr.globalstat = "Below 145 (END CYCLE)"
            [dmgr.get(t).setLEDs(0) for t in thermostats]
            dmgr.get('woodcirc').set(1)
            dmgr.get('wooddraft').set(0)            
        else:
            # Below 145 we try to preserve coals
            dmgr.globalstat = "Below 145 (Preserving Coals)"
            [dmgr.get(t).setLEDs(2) for t in thermostats]
            dmgr.get('woodcirc').set(0)
            dmgr.get('wooddraft').set(0)

    elif boilertemp < 165:
        if endcycle.state is 1:
            dmgr.globalstat = "Below 165 (END CYCLE)"
            [dmgr.get(t).setLEDs(0) for t in thermostats]
            dmgr.get('woodcirc').set(1)
            dmgr.get('wooddraft').set(0)            
        else:
            # Below 165 we get the fire going
            dmgr.globalstat = "Below 165 (Firing)"
            coldstart.setState(0)
            [dmgr.get(t).setLEDs(2) for t in thermostats]
            dmgr.get('woodcirc').set(0)
            dmgr.get('wooddraft').set(USEDRAFT)

    elif boilertemp < 185:
        # From 165-186 we are demand driven. At the moment, "demand" is the
        # "front room thermostat" until we add more logic.
        [dmgr.get(t).setLEDs(1) for t in thermostats]
        coldstart.setState(0)

        if (demand):
            dmgr.globalstat = "Demand (Firing/Circulating)"
            dmgr.get('woodcirc').set(1)
            dmgr.get('wooddraft').set(USEDRAFT)
        else:
            dmgr.globalstat = "No Demand (Standby)"
            dmgr.get('woodcirc').set(0)
            dmgr.get('wooddraft').set(0)

    elif boilertemp < 195:
        dmgr.globalstat = "High Limit, Circulating"
        [dmgr.get(t).setLEDs(1) for t in thermostats]
        dmgr.get('woodcirc').set(1)
        dmgr.get('wooddraft').set(0)

    else:
        dmgr.globalstat = "Overheat (Dumping)"
        [dmgr.get(t).setLEDs(4) for t in thermostats]
        dmgr.get('woodcirc').set(1)
        dmgr.get('wooddraft').set(0)

    status = "upstairs,%.2f\n\
downstairs,%.2f\n\
frontroom,%.2f\n\
boiler,%.2f\n\
return,%.2f\n\
mode,%s\n\
devices,Circ: %s Draft: %s\n" % (
        tstatbed.status['temp'],
        tstatdown.status['temp'],
        tstatfront.status['temp'],
        dmgr.get('boilertemp').status['temperature'],
        dmgr.get('returntemp').status['temperature'],
        dmgr.globalstat,
        'ON' if dmgr.get('woodcirc').status['output'] is 1 else 'OFF',
        'ON' if dmgr.get('wooddraft').status['output'] is 1 else 'OFF')

    writeFileValue('/var/run/hotpi/status', status)

    time.sleep(10)

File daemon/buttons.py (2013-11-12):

# apt-get install python-rpi.gpio
# pip install i2c
# pip install smbus


#import RPi.GPIO as GPIO

#GPIO.setmode(GPIO.BCM)

#GPIO.setup(17, GPIO.IN)

import smbus
import time

bus = smbus.SMBus(0)  # Rev 1 Pi uses 0
#bus = smbus.SMBus(1) # Rev 2 Pi uses 1

DEVICE = 0x22  # Device address (A0-A2)
IODIRA = 0x00  # Pin direction register
GPIOA = 0x12  # Register for inputs

# Set all GPB pins as outputs
# bus.write_byte_data(DEVICE, IODIRB, ...)

# Set first 7 GPA pins as outputs and
# last one as input.
#bus.write_byte_data(DEVICE,IODIRA,0x80)

# Set all GPA pins as inputs
bus.write_byte_data(DEVICE, IODIRA, 0xFF)

# Loop until user presses CTRL-C
while True:
    # Read state of GPIOA register
    MySwitch = bus.read_byte_data(DEVICE, GPIOA)

    # blue: 111100
    print "{0:b}".format(MySwitch)

    if MySwitch & 0b10000000 == 0b10000000:
        print "Switch was pressed!"

    time.sleep(0.5)

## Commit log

2012-09-17 Flesh out repository
    [Bottom.gbr, BottomMask.gbr, Through.gbr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]
2012-09-17 PCB Readme
2012-09-27 Basic Teensy project
2012-10-01 TeensyIO code
2012-10-24 Bug fixes, timer revisions, and general code improvements
2012-10-29 Bugfixes for PCB
2012-10-29 Bug fixes for Teensy interface board
2012-10-29 Re-produce Gerbers for fixed PCB design
    [Bottom.gbr, BottomMask.gbr, Through.nc.drl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]
2012-10-29 Add PDF of schematic
2012-12-28 Revision 2 PCBs, schematics, and Gerbers
    [hotpi-bom.csv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]
2013-01-01 Minor bug fixes on relay board.
2013-01-01 Bug fix (0805 -> 1206) on Thermocouple board.
2013-01-02 HotPi main board bug fixes
2013-01-13 Fix hole location on main boards
2013-01-26 Zone Controller PCB bug fix
2013-02-02 Begin re-routing Zone Controller
    [zone-bom.csv]
2013-04-19 Playing with option for zone relay.
2013-06-17 Tweaking board design.
2013-06-24 Tweak relay board layout.
2013-06-29 Update relay board with open drains
2013-08-31 Reworking main board with RS-232.
2013-09-01 PDF for new main schematic.
2013-09-01 Routed board to match.
2013-09-02 Finished Adjustments to HotPi Main Board.
    [hotpi-bom.csv]
2013-09-02 Rework zone/relay board around new design.
    [relay-bom.csv, zone-bom.csv]
2013-09-10 Level Sensor
    [analog-bom.csv]
2013-09-11 Level Sensor Files
    [level-bom.csv]
2013-09-11 Analog input board
2013-09-15 Optimized relay PCB for noise reduction.
2013-09-15 Prepare boards for order.
2013-09-15 BOM updates.
    [analog-bom.csv]
2013-09-30 Relay board bug fixes, larger pads and holes.
2013-10-09 Bug fix for level detection board.
    [level-bom.csv]
2013-11-12 Relay board bug fixes
2013-11-12 Artwork for bug-fixed relay board
2014-10-07 PCB Updates, preparing for v3
    [analog-bom.csv, hotpi-bom.csv, level-bom.csv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]
2014-10-11 Zone board updates
2014-11-13 Slim output-only board
2014-11-13 Gerber and N/C drill files, BOM files
    [bom.csv, hotpi-bom.csv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]
